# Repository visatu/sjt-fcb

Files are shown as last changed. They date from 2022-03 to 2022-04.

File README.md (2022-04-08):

View this project on [CADLAB.io](https://cadlab.io/project/25264).

**PRELIMINARY DESIGN - NOT TESTED - YET**

# sjt-fcb

Drone flight controller designed for hobbyist use. Designed as a part of an embedded design course.

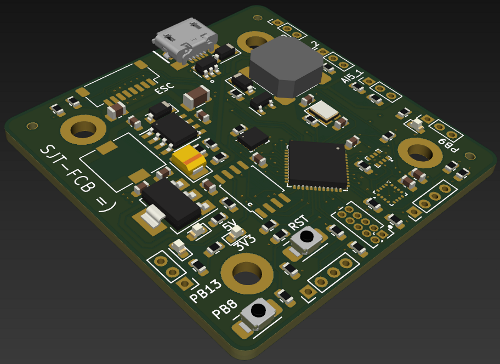
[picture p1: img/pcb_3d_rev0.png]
Some parts are missing 3D models


## Features

| Component | Desc |
| --- | --- |
| CPU | [ST STM32F411CEU6](https://www.st.com/resource/en/datasheet/stm32f411ce.pdf) |
| IMU | [ST LSM6DS3](https://content.arduino.cc/assets/st_imu_lsm6ds3_datasheet.pdf) |
| Onboard flash | 128 Mb SPI NOR |
| RF Module | [SiLabs SI4432](https://www.silabs.com/documents/public/data-sheets/Si4430-31-32.pdf) based 315 - 915 MHz [module](https://datasheet.lcsc.com/lcsc/1912111437_DreamLNK-DL-RTS4432-433M_C381165.pdf) |
| Barometer | [Infineon DPS310](https://www.infineon.com/dgdl/Infineon-DPS310-DataSheet-v01_02-EN.pdf?fileId=5546d462576f34750157750826c42242) |
| Magnetometer  | [QST QMC5883L ](https://datasheet.lcsc.com/lcsc/2012221837_QST-QMC5883L_C976032.pdf) |
| | |

- Designed to connect to a
[RaceStar 35A](https://www.racerstar.com/Anniversary-Special-Edition-Racerstar-REV35-35A-BLheli_S-3-6S-4-In-1-ESC-Built-in-Current-Sensor-for-RC-Drone-p-254.html) ESC
- 2.0 mm pitch connectors for external I/O
  - I2C
  - UART
  - 2 x 5V Analog input
  - 1 x 3V Analog input
  - 2 x GPIO
- USB 2.0 connection
- Onboard buzzer
- User programmable button :)

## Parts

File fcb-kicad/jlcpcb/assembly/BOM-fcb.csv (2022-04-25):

Comment | Designator | Footprint | LCSC
500mA 600Ω@100M | FB1 | C_0805_2012Metric | C1017
DPS310 | U7 | PG-VLGA-8-1 | C130156
10u 50V | C2 | C_1206_3216Metric | C13585
16 MHz | Y1 | Crystal_SMD_3225-4Pin_3.2x2.5mm | C13738
100n | C10,C14,C15,C16,C18,C21,C3,C5,C6,C7,C8 | C_0603_1608Metric | C14663
100u 6.3V | C11 | CP_EIA-3528-15_AVX-H_Pad1.50x2.35mm_HandSolder | C16133
6.8p | CL1,CL2 | C_0603_1608Metric | C1679
STM32F411CEUx | U1 | QFN-48-1EP_7x7mm_P0.5mm_EP5.6x5.6mm | C190642
4.7u | C1,C19,C4 | C_0603_1608Metric | C19666
10u 10V | C12,C13 | C_0603_1608Metric | C19702
220n | C20 | C_0603_1608Metric | C21120
1k | R13,R14,R2,R6 | R_0603_1608Metric | C21190
S8050 J3Y | Q1 | SOT-23 | C2146
LED_red | D3,D4 | LED_0603_1608Metric | C2286
470 | R25 | R_0603_1608Metric | C23179
5.1k | R26,R28 | R_0603_1608Metric | C23186
22 | R10,R7,R8,R9 | R_0603_1608Metric | C23345
240 | R23,R24,R5 | R_0603_1608Metric | C23350
10k | R1,R11,R12,R15,R16,R17,R18,R19,R20,R21,R22,R27,R29,R3 | R_0603_1608Metric | C25804
3k | R4 | R_0603_1608Metric | C4211
10n | C9 | C_0603_1608Metric | C57112
AMS1117-3.3 | U3 | SOT-223-3_TabPin2 | C6186
Blue, 3V | D5,D6 | LED_0603_1608Metric | C72041
1N4148W | D7 | D_SOD-123 | C81598
SRV05-4 | U9 | SOT-23-6 | C85364
B5819W SL | D1,D2 | D_SOD-123 | C8598
LSM6DS3 | U5 | LGA-14_3x2.5mm_P0.5mm_LayoutBorder3x4y | C95230
W25Q128JVS | U4 | SOIC-8_5.23x5.23mm_P1.27mm | C97521
QMC5883L | U8 | QMC5883L | C976032
TPS5430DDA | U2 | TI_SO-PowerPAD-8_ThermalVias | C9864

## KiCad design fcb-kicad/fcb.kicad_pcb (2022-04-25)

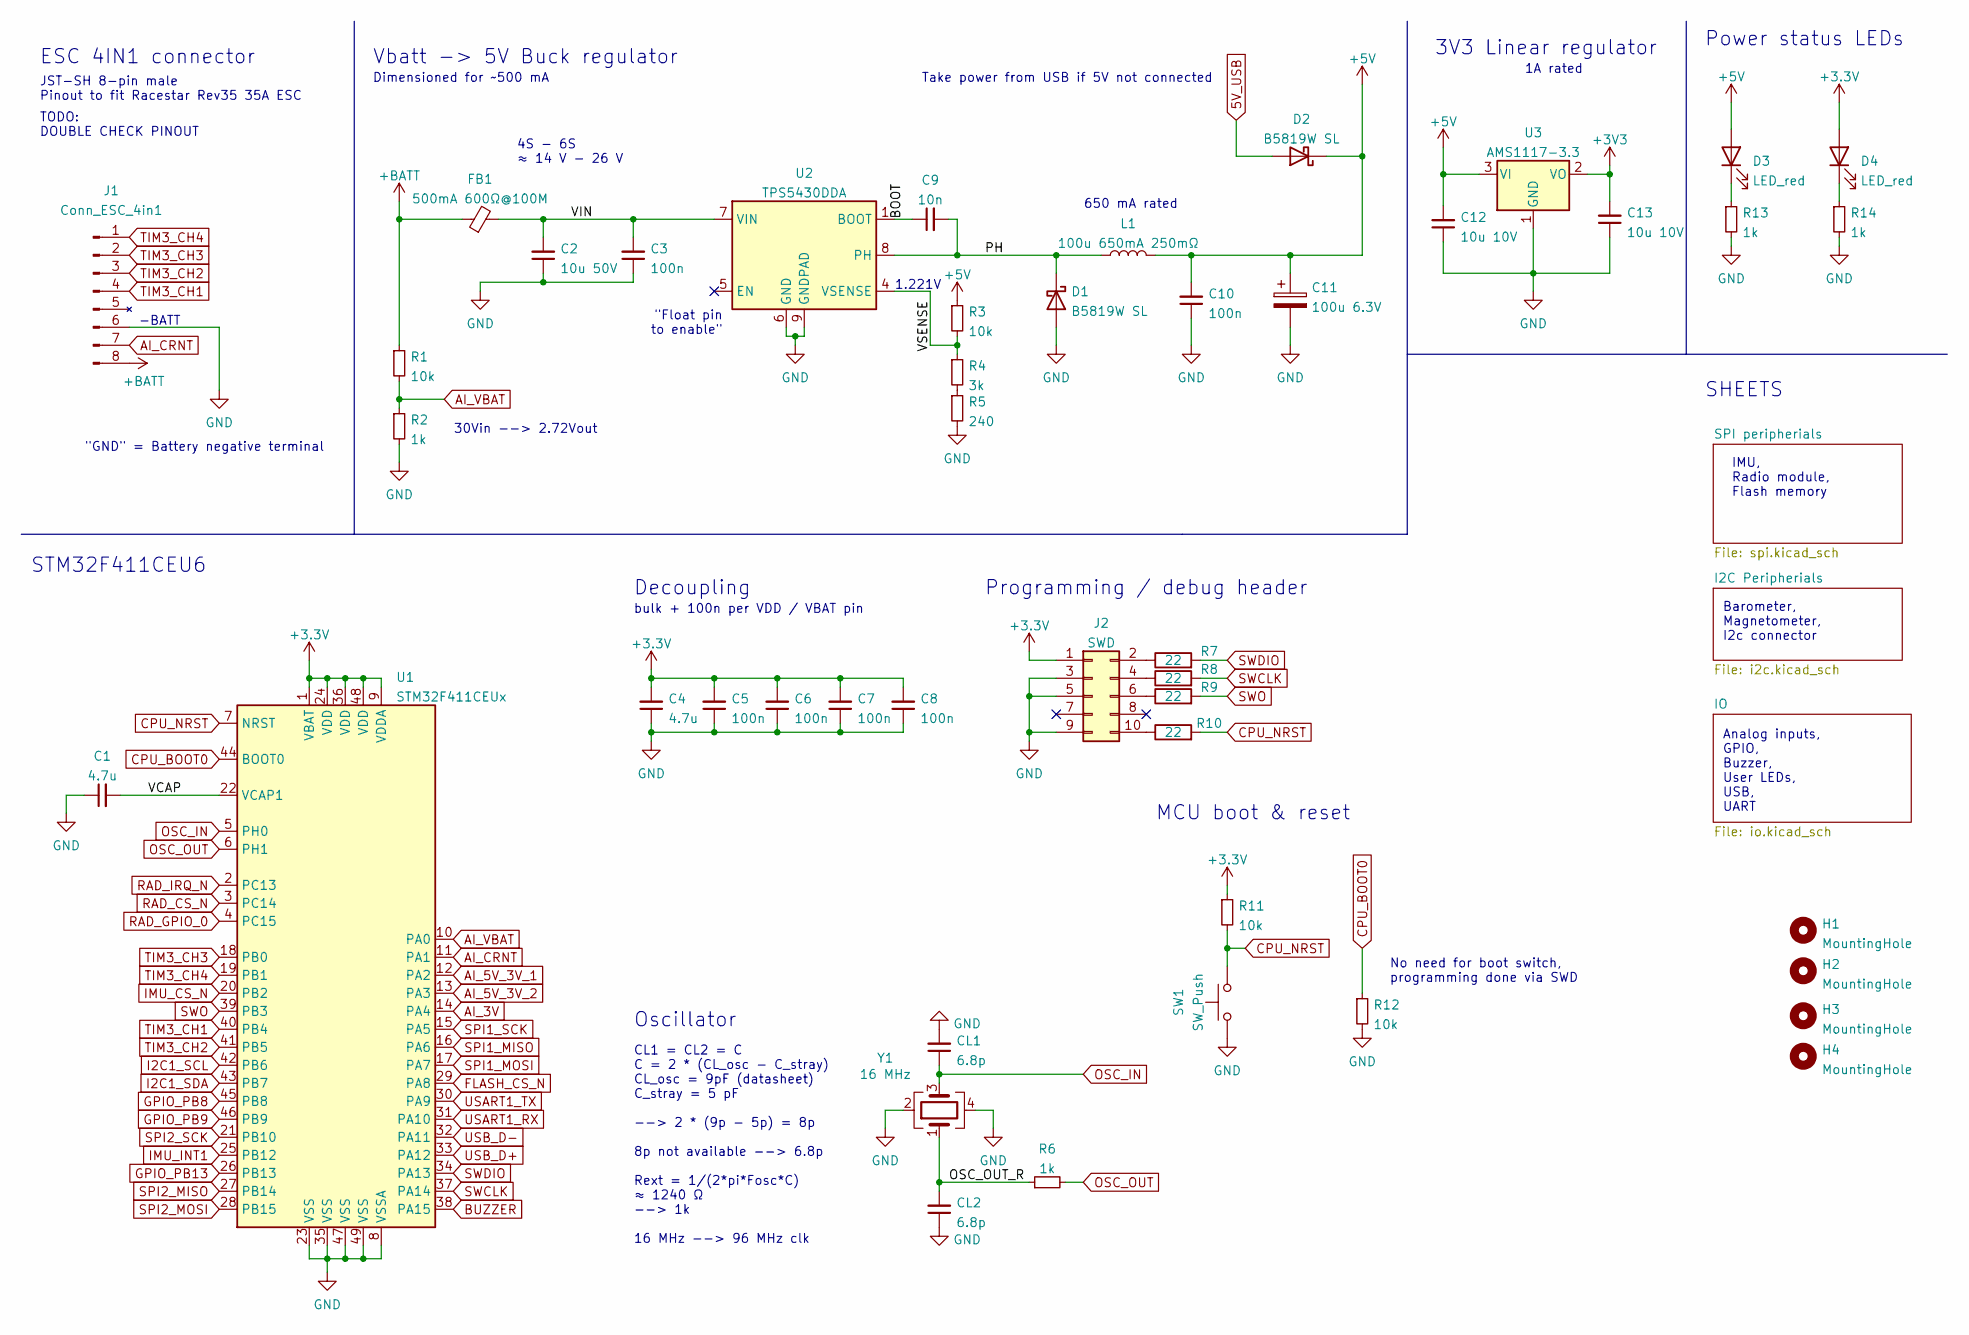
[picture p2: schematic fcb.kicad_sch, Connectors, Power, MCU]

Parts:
C1, C4: 4.7u; C_0603_1608Metric; LCSC C19666
C2: 10u 50V; C_1206_3216Metric; LCSC C89632
C3, C5, C6, C7, C8, C10: 100n; C_0603_1608Metric; LCSC C14663
C9: 10n; C_0603_1608Metric; LCSC C57112
C11: 100u 6.3V; CP_EIA-3528-15_AVX-H_Pad1.50x2.35mm_HandSolder; LCSC C16133
C12, C13: 10u 10V; C_0603_1608Metric; LCSC C19702
CL1, CL2: 6.8p; C_0603_1608Metric; LCSC C1679
D1, D2: B5819W SL; D_SOD-123; LCSC C8598
D3, D4: LED_red; LED_0603_1608Metric; LCSC C84263
FB1: 500mA 600Ω@100M; C_0805_2012Metric; LCSC C1017
H1, H2, H3, H4: MountingHole; MountingHole_3.2mm_M3_DIN965_Pad
J1: Conn_ESC_4in1; JST_SH_SM08B-SRSS-TB_1x08-1MP_P1.00mm_Horizontal; LCSC C49633
J2: SWD; PinHeader_2x05_P1.27mm_Vertical; LCSC C2895038
L1: 100u 650mA 250mΩ; L_7.3x7.3_H4.5; LCSC C254876
R1, R3, R11, R12: 10k; R_0603_1608Metric; LCSC C25804
R2, R6, R13, R14: 1k; R_0603_1608Metric; LCSC C21190
R4: 3k; R_0603_1608Metric; LCSC C4211
R5: 240; R_0603_1608Metric; LCSC C23350
R7, R8, R9, R10: 22; R_0603_1608Metric; LCSC C23345
SW1: SW_Push; Button-2.9x4.0mm-SMD; LCSC C720477
U1: STM32F411CEUx; QFN-48-1EP_7x7mm_P0.5mm_EP5.6x5.6mm; LCSC C60420
U2: TPS5430DDA; TI_SO-PowerPAD-8_ThermalVias; LCSC C9864
U3: AMS1117-3.3; SOT-223-3_TabPin2; LCSC C6186
Y1: 16 MHz; Crystal_SMD_3225-4Pin_3.2x2.5mm; LCSC C13738

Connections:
5V_USB: D2.2 (A); also elsewhere on the board
+5V: C10.2, C11.1, C12.2, D2.1 (K), D3.2 (A), L1.2, R3.1, U3.3 (VI); also elsewhere on the board
+BATT: FB1.1, J1.8 (VBAT), R1.1
/BOOT: C9.1, U2.1 (BOOT)
/OSC_OUT_R: CL2.2, R6.1, Y1.1
/PH: C9.2, D1.1 (K), L1.1, U2.8 (PH)
/VCAP: C1.2, U1.22 (VCAP1)
/VIN: C2.2, C3.2, FB1.2, U2.7 (VIN)
/VSENSE: R3.2, R4.1, U2.4 (VSENSE)
AI_3V: U1.14 (PA4); also elsewhere on the board
AI_5V_3V_1: U1.12 (PA2); also elsewhere on the board
AI_5V_3V_2: U1.13 (PA3); also elsewhere on the board
AI_CRNT: J1.7 (CRNT), U1.11 (PA1)
AI_VBAT: R1.2, R2.1, U1.10 (PA0)
BUZZER: U1.38 (PA15); also elsewhere on the board
CPU_BOOT0: R12.1, U1.44 (BOOT0)
CPU_NRST: R10.2, R11.2, SW1.2, U1.7 (NRST)
FLASH_CS_N: U1.29 (PA8); also elsewhere on the board
GND: C1.1, C2.1, C3.1, C4.1, C5.1, C6.1, C7.1, C8.1, C10.1, C11.2, C12.1, C13.1, CL1.2, CL2.1, D1.2 (A), J1.6 (GND), J2.3, J2.5, J2.9, R2.2, R5.2, R12.2, R13.2, R14.2, SW1.1, U1.8 (VSSA), U1.23 (VSS), U1.35 (VSS), U1.47 (VSS), U1.49 (VSS), U2.6 (GND), U2.9 (GNDPAD), U3.1 (GND), Y1.2, Y1.4; also elsewhere on the board
GPIO_PB8: U1.45 (PB8); also elsewhere on the board
GPIO_PB9: U1.46 (PB9); also elsewhere on the board
GPIO_PB13: U1.26 (PB13); also elsewhere on the board
I2C1_SCL: U1.42 (PB6); also elsewhere on the board
I2C1_SDA: U1.43 (PB7); also elsewhere on the board
IMU_CS_N: U1.20 (PB2); also elsewhere on the board
IMU_INT1: U1.25 (PB12); also elsewhere on the board
unnamed: D3.1 (K), R13.1
unnamed: D4.1 (K), R14.1
unnamed: J2.2, R7.1
unnamed: J2.4, R8.1
unnamed: J2.6, R9.1
unnamed: J2.10, R10.1
unnamed: R4.2, R5.1
OSC_IN: CL1.1, U1.5 (PH0), Y1.3
OSC_OUT: R6.2, U1.6 (PH1)
RAD_CS_N: U1.3 (PC14); also elsewhere on the board
RAD_GPIO_0: U1.4 (PC15); also elsewhere on the board
RAD_IRQ_N: U1.2 (PC13); also elsewhere on the board
SPI1_MISO: U1.16 (PA6); also elsewhere on the board
SPI1_MOSI: U1.17 (PA7); also elsewhere on the board
SPI1_SCK: U1.15 (PA5); also elsewhere on the board
SPI2_MISO: U1.27 (PB14); also elsewhere on the board
SPI2_MOSI: U1.28 (PB15); also elsewhere on the board
SPI2_SCK: U1.21 (PB10); also elsewhere on the board
SWCLK: R8.2, U1.37 (PA14)
SWDIO: R7.2, U1.34 (PA13)
SWO: R9.2, U1.39 (PB3)
TIM3_CH1: J1.4 (IN1), U1.40 (PB4)
TIM3_CH2: J1.3 (IN2), U1.41 (PB5)
TIM3_CH3: J1.2 (IN3), U1.18 (PB0)
TIM3_CH4: J1.1 (IN4), U1.19 (PB1)
USART1_RX: U1.31 (PA10); also elsewhere on the board
USART1_TX: U1.30 (PA9); also elsewhere on the board
USB_D+: U1.33 (PA12); also elsewhere on the board
USB_D-: U1.32 (PA11); also elsewhere on the board

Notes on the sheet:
Power status LEDs
MCU boot & reset
Barometer, Magnetometer, I2c connector
Vbatt -> 5V Buck regulator
STM32F411CEU6
JST-SH 8-pin male Pinout to fit Racestar Rev35 35A ESC
30Vin --> 2.72Vout
Programming / debug header
1A rated
3V3 Linear regulator
Decoupling
"Float pin to enable"
Take power from USB if 5V not connected
-BATT
Dimensioned for ~500 mA
"GND" = Battery negative terminal
ESC 4IN1 connector
Analog inputs, GPIO, Buzzer, User LEDs, USB, UART
SHEETS
Oscillator
650 mA rated
4S - 6S ≈ 14 V - 26 V
bulk + 100n per VDD / VBAT pin
1.221V
CL1 = CL2 = C C = 2 * (CL_osc - C_stray) CL_osc = 9pF (datasheet) C_stray = 5 pF --> 2 * (9p - 5p) = 8p 8p not available --> 6.8p Rext = 1/(2*pi*Fosc*C) ≈ 1240 Ω --> 1k 16 MHz --> 96 MHz clk
No need for boot switch, programming done via SWD
IMU, Radio module, Flash memory
TODO: DOUBLE CHECK PINOUT

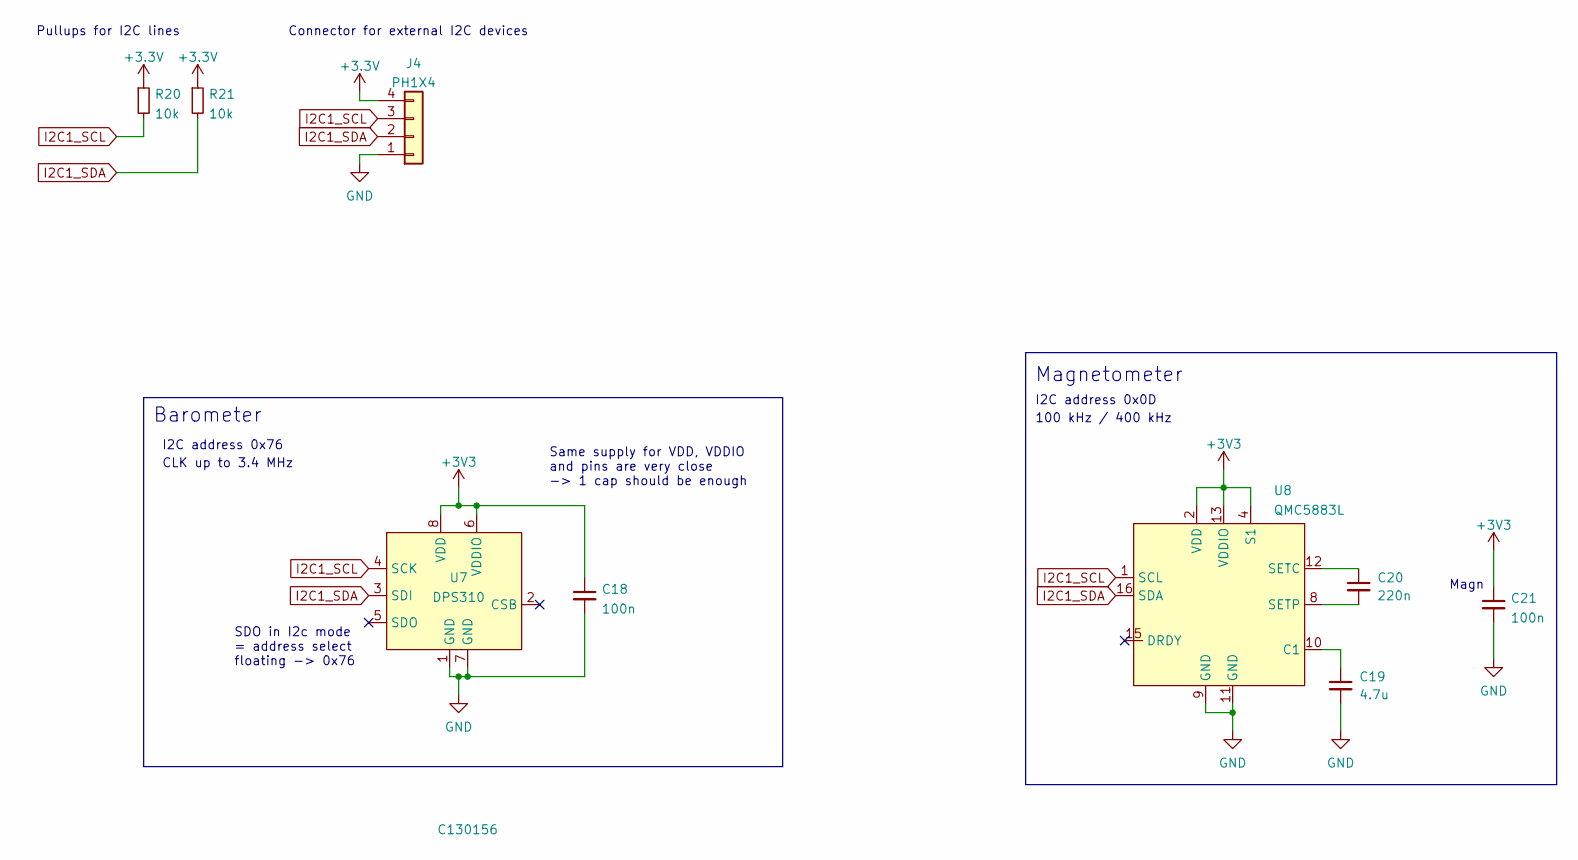
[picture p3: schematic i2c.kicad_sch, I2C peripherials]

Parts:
C18, C21: 100n; C_0603_1608Metric; LCSC C14663
C19: 4.7u; C_0603_1608Metric; LCSC C19666
C20: 220n; C_0603_1608Metric; LCSC C21120
J4: PH1X4; PinHeader_1x04_P2.00mm_Vertical; LCSC C388723
R20, R21: 10k; R_0603_1608Metric; LCSC C25804
U7: DPS310; PG-VLGA-8-1; LCSC C130156
U8: QMC5883L; LCSC C976032

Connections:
GND: C18.2, C19.2, C21.2, J4.1, U7.1 (GND), U7.7 (GND), U8.9 (GND), U8.11 (GND); also elsewhere on the board
I2C1_SCL: J4.3, R20.2, U7.4 (SCK), U8.1 (SCL); also elsewhere on the board
I2C1_SDA: J4.2, R21.2, U7.3 (SDI), U8.16 (SDA); also elsewhere on the board
unnamed: C19.1, U8.10 (C1)
unnamed: C20.1, U8.12 (SETC)
unnamed: C20.2, U8.8 (SETP)

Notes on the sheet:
Pullups for I2C lines
SDO in I2c mode = address select floating -> 0x76
CLK up to 3.4 MHz
I2C address 0x0D
Connector for external I2C devices
Magnetometer
100 kHz / 400 kHz
Same supply for VDD, VDDIO and pins are very close -> 1 cap should be enough
I2C address 0x76
Barometer
Magn

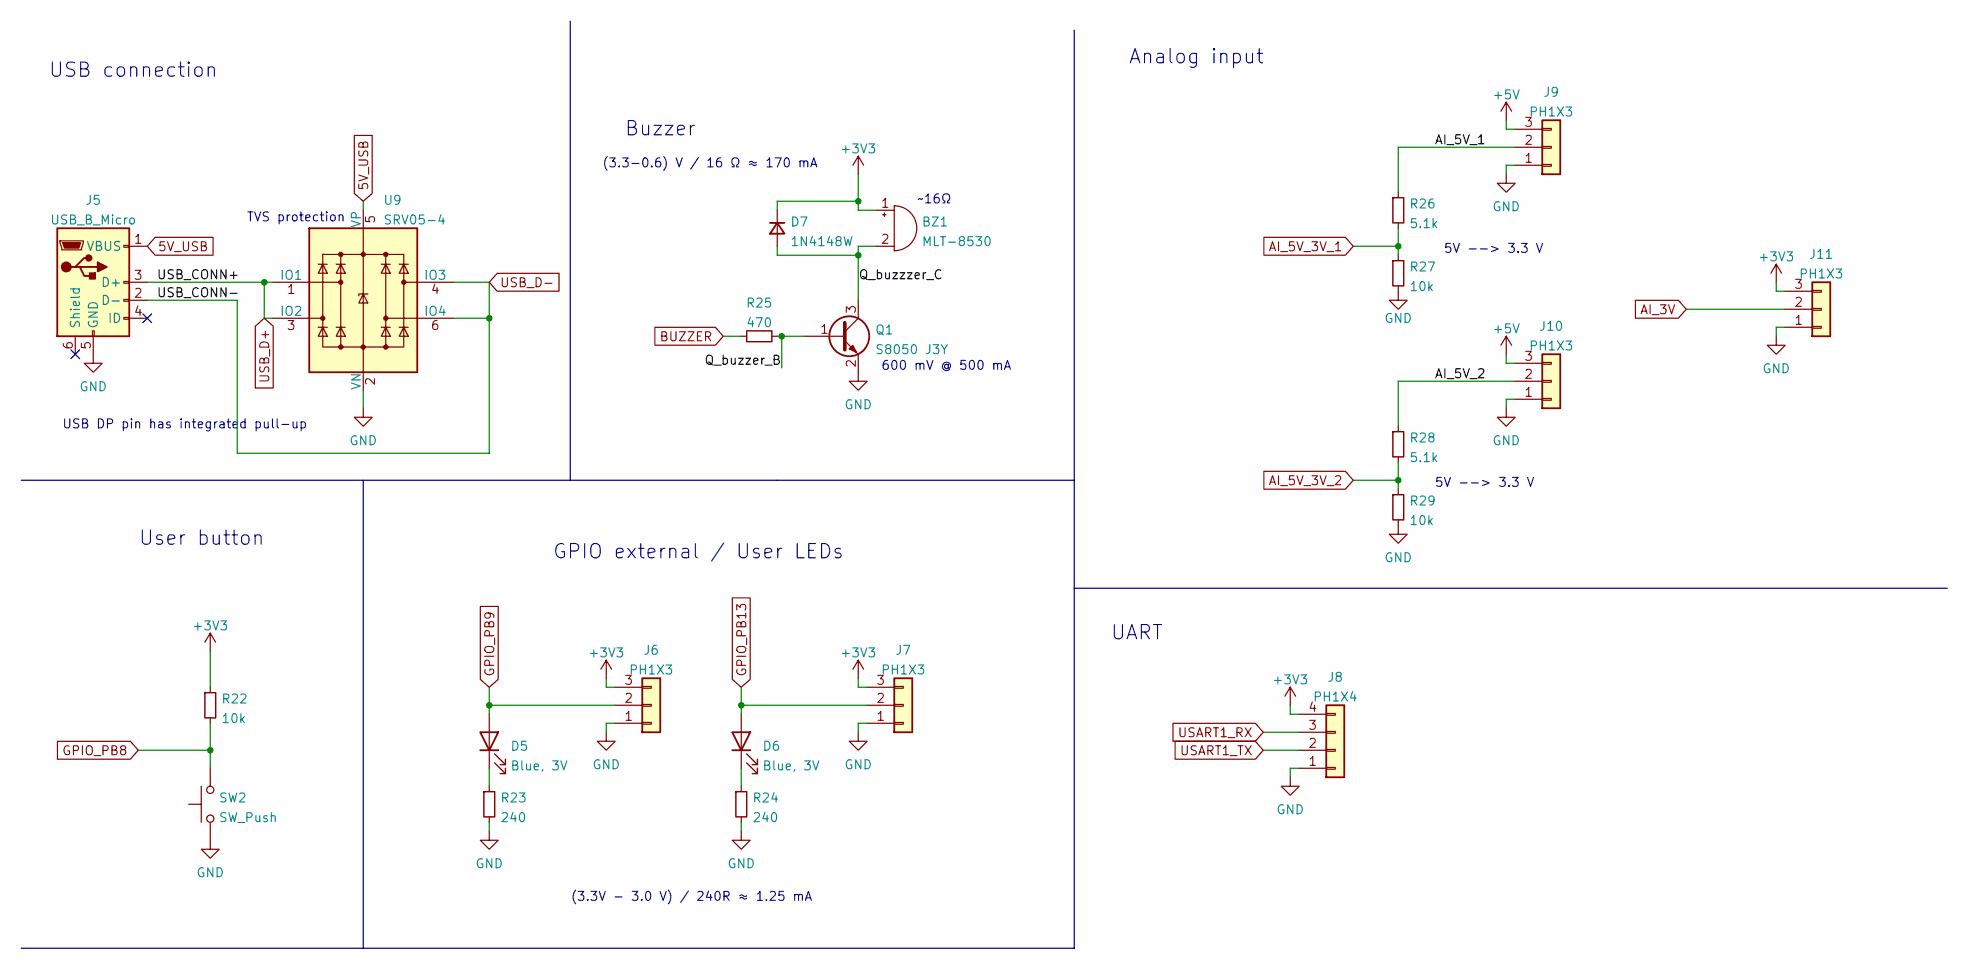
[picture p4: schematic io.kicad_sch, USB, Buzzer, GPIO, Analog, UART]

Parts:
BZ1: MLT-8530; MLT-8350; LCSC C94599
D5, D6: Blue, 3V; LED_0603_1608Metric; LCSC C72041
D7: 1N4148W; D_SOD-123; LCSC C81598
J5: USB_B_Micro; MICRO-USB-SMD_U254-051T-4BH83-F1S; LCSC C397452
J6, J7, J9, J10, J11: PH1X3; PinHeader_1x03_P2.00mm_Vertical; LCSC C571312
J8: PH1X4; PinHeader_1x04_P2.00mm_Vertical; LCSC C388723
Q1: S8050 J3Y; SOT-23; LCSC C2146
R22, R27, R29: 10k; R_0603_1608Metric; LCSC C25804
R23, R24: 240; R_0603_1608Metric; LCSC C23350
R25: 470; R_0603_1608Metric; LCSC C23179
R26, R28: 5.1k; R_0603_1608Metric; LCSC C23186
SW2: SW_Push; Button-2.9x4.0mm-SMD; LCSC C720477
U9: SRV05-4; SOT-23-6; LCSC C85364

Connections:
5V_USB: J5.1 (VBUS), U9.5 (VP); also elsewhere on the board
+5V: J9.3, J10.3; also elsewhere on the board
/IO/AI_5V_1: J9.2, R26.1
/IO/AI_5V_2: J10.2, R28.1
/IO/Q_buzzer_B: Q1.1 (B), R25.2
/IO/Q_buzzzer_C: BZ1.2 (+), D7.2 (A), Q1.3 (C)
AI_3V: J11.2; also elsewhere on the board
AI_5V_3V_1: R26.2, R27.1; also elsewhere on the board
AI_5V_3V_2: R28.2, R29.1; also elsewhere on the board
BUZZER: R25.1; also elsewhere on the board
GND: J5.5 (GND), J6.1, J7.1, J8.1, J9.1, J10.1, J11.1, Q1.2 (E), R23.2, R24.2, R27.2, R29.2, SW2.1, U9.2 (VN); also elsewhere on the board
GPIO_PB8: R22.2, SW2.2; also elsewhere on the board
GPIO_PB9: D5.2 (A), J6.2; also elsewhere on the board
GPIO_PB13: D6.2 (A), J7.2; also elsewhere on the board
unnamed: D5.1 (K), R23.1
unnamed: D6.1 (K), R24.1
USART1_RX: J8.3; also elsewhere on the board
USART1_TX: J8.2; also elsewhere on the board
USB_D+: J5.3 (D+), U9.1 (IO1), U9.3 (IO2); also elsewhere on the board
USB_D-: J5.2 (D-), U9.4 (IO3), U9.6 (IO4); also elsewhere on the board

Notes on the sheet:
USB connection
User button
(3.3V - 3.0 V) / 240R ≈ 1.25 mA
USB DP pin has integrated pull-up
Analog input
Buzzer
GPIO external / User LEDs
5V --> 3.3 V
UART
TVS protection
~16Ω
600 mV @ 500 mA
(3.3-0.6) V / 16 Ω ≈ 170 mA

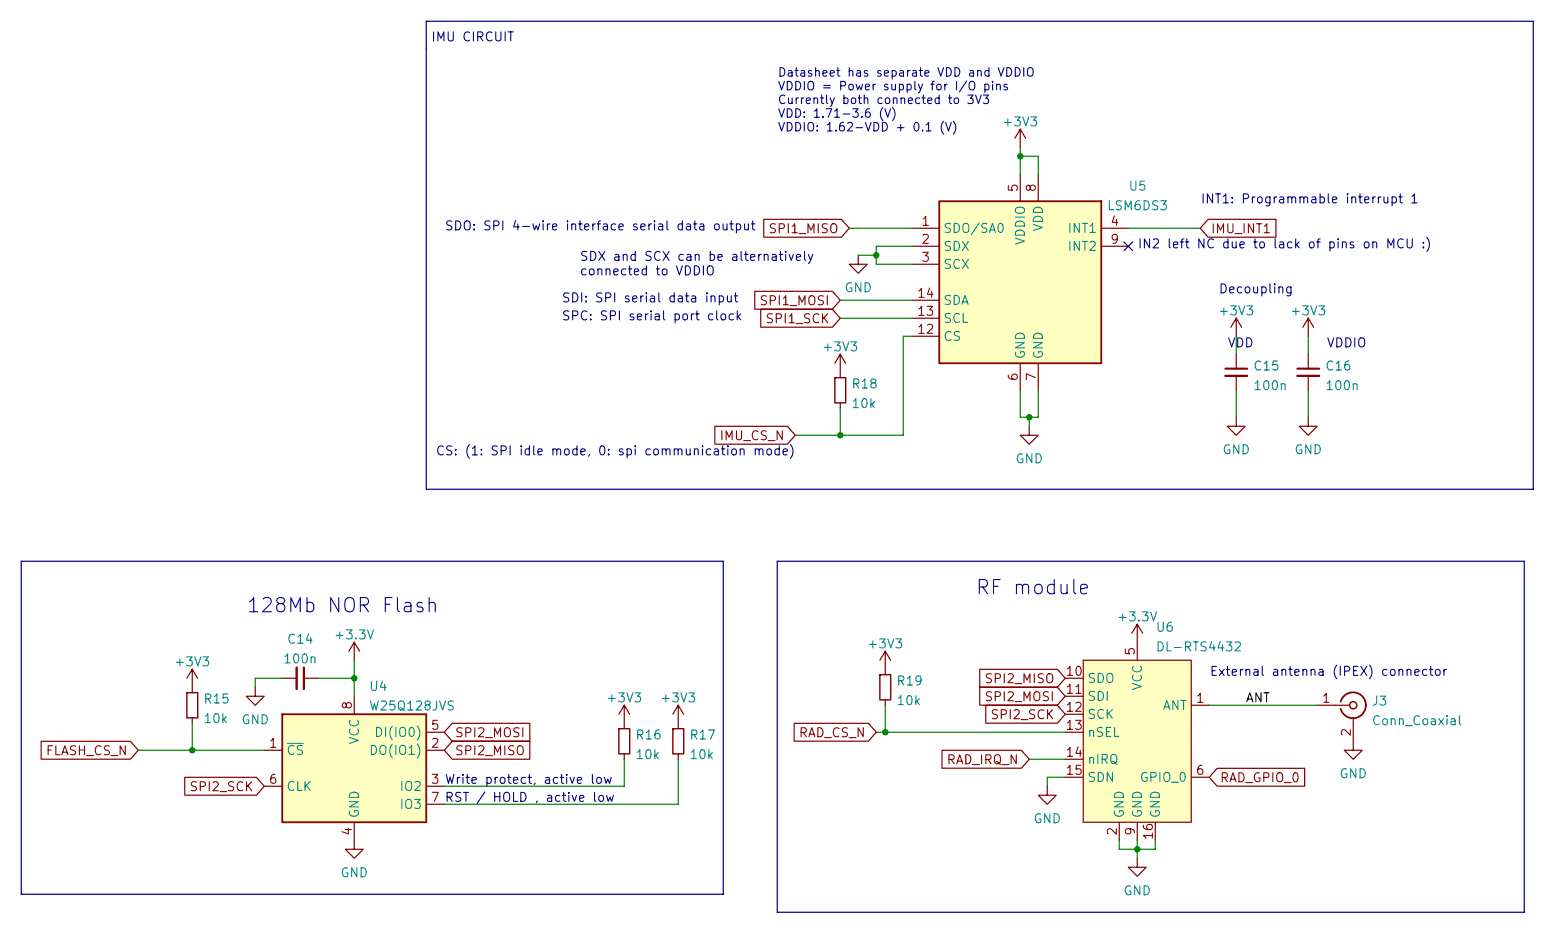
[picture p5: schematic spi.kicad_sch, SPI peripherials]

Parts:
C14, C15, C16: 100n; C_0603_1608Metric; LCSC C14663
J3: Conn_Coaxial; KH-IPEX-K501-29; LCSC C411563
R15, R16, R17, R18, R19: 10k; R_0603_1608Metric; LCSC C25804
U4: W25Q128JVS; SOIC-8_5.23x5.23mm_P1.27mm; LCSC C97521
U5: LSM6DS3; LGA-14_3x2.5mm_P0.5mm_LayoutBorder3x4y; LCSC C95230
U6: DL-RTS4432; DL-RTS4432_board; LCSC C381165

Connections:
/SPI peripherials/ANT: J3.1 (In), U6.1 (ANT)
FLASH_CS_N: R15.2, U4.1 (~CS); also elsewhere on the board
GND: C14.2, C15.2, C16.2, J3.2 (Ext), U4.4 (GND), U5.2 (SDX), U5.3 (SCX), U5.6 (GND), U5.7 (GND), U6.2 (GND), U6.9 (GND), U6.15 (SDN), U6.16 (GND); also elsewhere on the board
IMU_CS_N: R18.2, U5.12 (CS); also elsewhere on the board
IMU_INT1: U5.4 (INT1); also elsewhere on the board
unnamed: R16.2, U4.3 (IO2)
unnamed: R17.2, U4.7 (IO3)
RAD_CS_N: R19.2, U6.13 (nSEL); also elsewhere on the board
RAD_GPIO_0: U6.6 (GPIO_0); also elsewhere on the board
RAD_IRQ_N: U6.14 (nIRQ); also elsewhere on the board
SPI1_MISO: U5.1 (SDO/SA0); also elsewhere on the board
SPI1_MOSI: U5.14 (SDA); also elsewhere on the board
SPI1_SCK: U5.13 (SCL); also elsewhere on the board
SPI2_MISO: U4.2 (DO(IO1)), U6.10 (SDO); also elsewhere on the board
SPI2_MOSI: U4.5 (DI(IO0)), U6.11 (SDI); also elsewhere on the board
SPI2_SCK: U4.6 (CLK), U6.12 (SCK); also elsewhere on the board

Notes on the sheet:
Write protect, active low
CS: (1: SPI idle mode, 0: spi communication mode)
SDO: SPI 4-wire interface serial data output
RST / HOLD , active low
Decoupling
SDI: SPI serial data input
SDX and SCX can be alternatively connected to VDDIO
128Mb NOR Flash
IMU CIRCUIT
VDDIO
IN2 left NC due to lack of pins on MCU :)
External antenna (IPEX) connector
SPC: SPI serial port clock
Datasheet has separate VDD and VDDIO VDDIO = Power supply for I/O pins Currently both connected to 3V3 VDD: 1.71-3.6 (V) VDDIO: 1.62-VDD + 0.1 (V)
VDD
RF module
INT1: Programmable interrupt 1

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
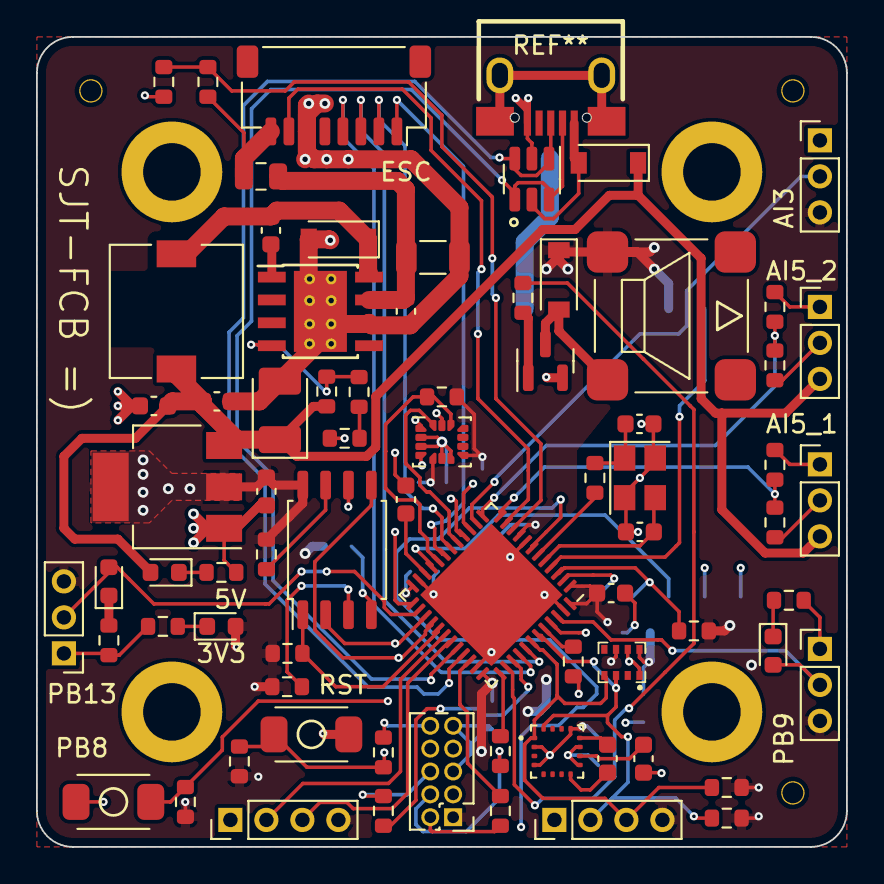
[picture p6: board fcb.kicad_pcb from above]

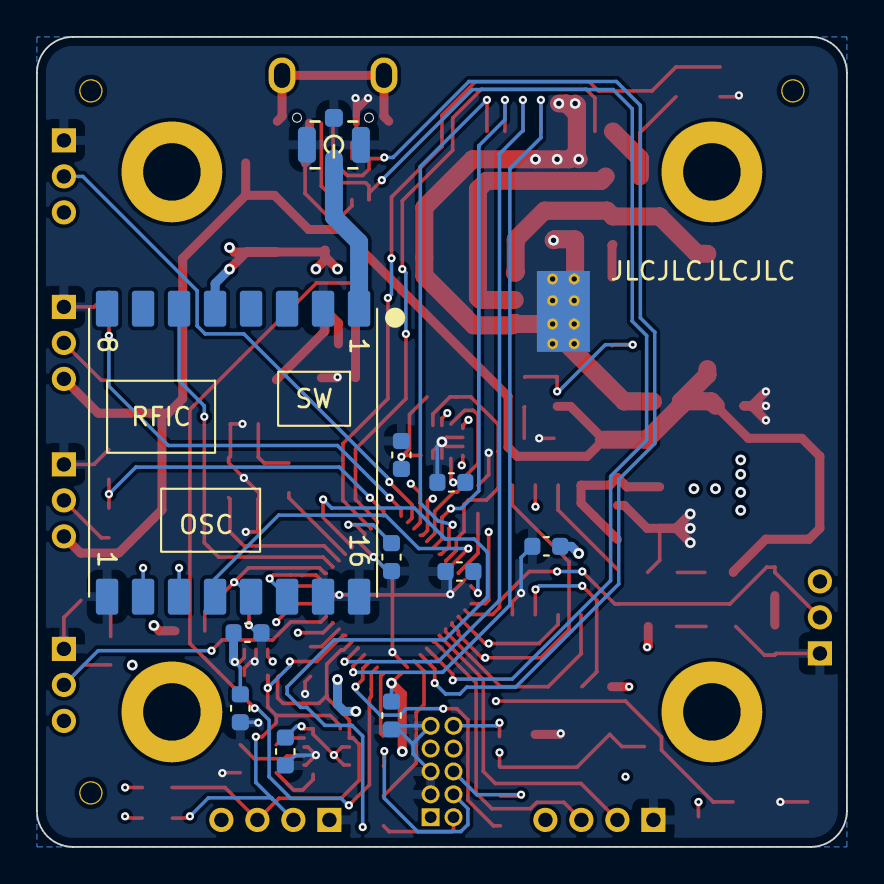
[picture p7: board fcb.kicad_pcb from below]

Board: 4 copper layers, 45.0 x 45.0 mm, 92 parts (11 on the bottom side), 68 nets.

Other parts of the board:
T1, T2, T3: JLCPCB_NPTH

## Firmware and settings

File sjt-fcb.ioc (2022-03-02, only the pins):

Mcu.UserName=STM32F411CEUx
PA0-WKUP.GPIO_Label=AI_VBAT
PA0-WKUP.Signal=ADCx_IN0
PA1.GPIO_Label=AI_CRNT
PA1.Signal=ADCx_IN1
PA10.Signal=USART1_RX
PA11.Signal=USB_OTG_FS_DM
PA12.Signal=USB_OTG_FS_DP
PA13.Signal=SYS_JTMS-SWDIO
PA14.Signal=SYS_JTCK-SWCLK
PA15.GPIO_Label=BUZZER
PA15.Signal=GPIO_Output
PA2.GPIO_Label=AI_5V_1
PA2.Signal=ADCx_IN2
PA3.GPIO_Label=AI_5V_2
PA3.Signal=ADCx_IN3
PA4.GPIO_Label=AI_3V
PA4.Signal=ADCx_IN4
PA5.Signal=SPI1_SCK
PA6.Signal=SPI1_MISO
PA7.Signal=SPI1_MOSI
PA8.GPIO_Label=FLASH_CS_N
PA8.Signal=GPIO_Output
PA9.Signal=USART1_TX
PB0.Signal=S_TIM3_CH3
PB1.Signal=S_TIM3_CH4
PB10.Signal=SPI2_SCK
PB12.GPIO_Label=IMU_INT1
PB12.Signal=GPIO_Input
PB13.Signal=GPIO_Output
PB14.Signal=SPI2_MISO
PB15.Signal=SPI2_MOSI
PB2.GPIO_Label=IMU_CS
PB2.Signal=GPIO_Output
PB3.Signal=SYS_JTDO-SWO
PB4.Signal=S_TIM3_CH1
PB5.Signal=S_TIM3_CH2
PB6.Signal=I2C1_SCL
PB7.Signal=I2C1_SDA
PB8.Signal=GPIO_Input
PB9.Signal=GPIO_Input
PC13-ANTI_TAMP.GPIO_Label=RAD_IRQ_N
PC13-ANTI_TAMP.Signal=GPXTI13
PC14-OSC32_IN.GPIO_Label=RAD_CS_N
PC14-OSC32_IN.Signal=GPIO_Output
PC15-OSC32_OUT.GPIO_Label=RAD_GPIO_0
PC15-OSC32_OUT.Signal=GPIO_Output

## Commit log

2022-02-28 gitignore kicad template
2022-02-28 alku säätöä.
    [fcb.kicad_sch]
2022-03-02 kicad into folder :)
    [fcb.kicad_pcb, fcb.kicad_sch]
2022-03-02 BMP388 footprint + 3D
2022-03-02 Added BMP388 symbol
    [fcb.kicad_sch]
2022-03-02 cpu pins
    [fcb.kicad_pcb, fcb.kicad_sch, i2c.kicad_sch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]
2022-03-02 hierarchic schemas, paljon muuta kivaa
    [fcb.kicad_pcb, fcb.kicad_sch, i2c.kicad_sch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]
2022-03-02 magnetometer symbol
2022-03-02 4in1 connector library part, SPI CS pullups, migrate magnetometer cirtuit
    [fcb.kicad_sch, i2c.kicad_sch, io.kicad_sch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]
2022-03-04 buzzer footprint
    [fcb.kicad_pcb, fcb.kicad_sch]
2022-03-06 buzzer notes
    [fcb.kicad_sch, i2c.kicad_sch, io.kicad_sch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]
2022-03-09 Analog inputs, connectors to GPIO
    [fcb.kicad_sch, io.kicad_sch]
2022-03-15 Schema rev0 done, Layout components grouped
    [fcb.kicad_pcb, fcb.kicad_sch, i2c.kicad_sch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]
2022-03-16 PCB rev0: "Babby's first Leiska"
    [fcb.kicad_pcb, fcb.kicad_sch, i2c.kicad_sch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]
2022-03-16 USB diffpair to bottom layer for more continous 3V3 fill
    [fcb.kicad_pcb]
2022-03-28 Less routing on inner layers, fabrication, BOM should be OK
    [BOM-fcb.csv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]
2022-04-08 wider pads for barometer footprint
    [fcb-CuBottom.gbr, fcb-CuIn1.gbr, fcb-CuIn2.gbr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]
2022-04-25 Change MCU to STM32F411CCU6
    [BOM-fcb.csv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]
2022-05-16 Interactive HTML BOM
